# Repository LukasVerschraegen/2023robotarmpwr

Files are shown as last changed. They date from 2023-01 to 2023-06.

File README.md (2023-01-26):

# 2023robotarmpwr

Doelstelling:
ontwerpen en programmeren van een robotarm. En het ontwerpen yan dels stüring voor de steppermotoren
Het
op basis van een micro controlletalie draadloos kan bediend worden. En eventueel een extra display kan worden
toegevoegd ter visualisatie van de instelbare parameters.
De robot zal een automatisatierobot zijn die éénmalig wordt ingesteld en zo repetitive taken kan uitvoeren. Je kan
verschillende taken en cyclussen aanmaken die dan kunnen worden geselecteerd uit het menu op het display. Het
instellen van een cyclus kan handmatig gebeuren via het display, of via code.De volledige constructie van de
robot zal worden uitgewerkt met de 3D-printer,

Verplichte onderdelen rapport:

Kaft (voorblad)                                                                                              (gebruik de recentste logo's)
Abstract (in het Engels en informatief)
Inhoudsopgave                                                                                             
Codefragmentenlijst                                                                                           
Figurenlijst
Tabellenlijst
Afkortingenlijst
Inleiding                                                                                                        
1 Hoofdstuktitel                                                                                             
2 ...                                                                                                                 
3 ...
4 ...                                                                       
Conclusie
Handleiding   (enkel verplicht indien laboproeven moeten geschreven worden, dan horen ze hier / indien het project in gebruik genomen zal worden, schrijf dan een handleiding)
Literatuurlijst
Bijlagenoverzicht  (opmaak zoals inhoudsopgave)
Bijlage 1: Kopieën datasheets
Bijlage 2: Vergaderverslagen
Bijlage 3:  Logboek rapporteren

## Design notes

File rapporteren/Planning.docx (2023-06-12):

## Academiejaar: 2022 / 2023

Planning PWR:

Verslaggever: Lukas Verschraegen, Lennert De Geeter, Jorik Van Dorpe, Roy De Volder

Klas: 3ELO

Lector: Mario Wyns

Lesweek 9: 27/02 - 5/03

Naam student: | Doel:
Lennert De Geeter | Ontwerp 3d print/mechanica
Roy De Volder | Componenten zoeken
Jorik Van Dorpe | Componenten zoeken
Lukas Verschraegen | Componenten zoeken

Lesweek 10: 6/03 - 12/03

Naam student: | Doel:
Lennert De Geeter | Ontwerp 3D print/mechanica
Roy De Volder | Componenten zoeken
Jorik Van Dorpe | Componenten zoeken
Lukas Verschraegen | Componenten zoeken

Lesweek 11: 13/03 - 19/03

Naam student: | Doel:
Lennert De Geeter | Ontwerp 3D print/mechanica
Roy De Volder | Componenten bestellen
Jorik Van Dorpe | Componenten bestellen
Lukas Verschraegen | Componenten bestellen

Lesweek 12: 20/03 - 26/03

Naam student: | Doel:
Lennert De Geeter | 3D prototyping
Roy De Volder | Mee helpen opstaren van schema
Jorik Van Dorpe | Starten van Programmatie
Lukas Verschraegen | Starten van schema

Lesweek 13: 27/03 - 2/04

Naam student: | Doel:
Lennert De Geeter | 3D prototyping
Roy De Volder | 3D print ontwerp helpen printen
Jorik Van Dorpe | Verder werken aan programmatie
Lukas Verschraegen | Verder werken aan schema

Lesweek 14: 3/04 - 9/04

Naam student: | Doel:
Lennert De Geeter | Printen + assemblage in 3D ontwerp
Roy De Volder | Pcb-design opstarten
Jorik Van Dorpe | Verder werken aan programmatie
Lukas Verschraegen | Afwerken schema

Lesweek 15: 10/04 - 16/04

Naam student: | Doel:
Lennert De Geeter | Printen + assemblage in 3D ontwerp
Roy De Volder | Verder werken aan pcb
Jorik Van Dorpe | Tussentest programma
Lukas Verschraegen | Afwerken schema

Lesweek 16: 17/04 - 23/04

Naam student: | Doel:
Lennert De Geeter | Printen + assemblage in 3D ontwerp
Roy De Volder | Verder werken pcb /opsturen
Jorik Van Dorpe | Tussentest programma
Lukas Verschraegen | Helpen afwerken pcb/ opsturen

Lesweek 17: 24/04 - 30/04

Naam student: | Doel:
Lennert De Geeter | Assemblage bouten en moeren
Roy De Volder | Wachten op printplaat = controle van elkaars werk en verder werken verslag
Jorik Van Dorpe | Wachten op printplaat = controle van elkaars werk en verder werken verslag
Lukas Verschraegen | Wachten op printplaat = controle van elkaars werk en verder werken verslag

Lesweek 18: 1/05 - 7/05

Naam student: | Doel:
Lennert De Geeter | Testen zonder motoren (alles draait)
Roy De Volder | Printplaat bestukken
Jorik Van Dorpe | Opstarten en testen pcb/ programmatie
Lukas Verschraegen | Opstarten en testen van pcb

Lesweek 19: 8/05 - 14/05

Naam student: | Doel:
Lennert De Geeter | Testen met motoren
Roy De Volder | Testen/ debuggen pcb
Jorik Van Dorpe | Testen/ debuggen code
Lukas Verschraegen | Testen/ debuggen schema

Lesweek 20: 15/05 - 21/05

Naam student: | Doel:
Lennert De Geeter | Herontwerp + assemblage
Roy De Volder | Testen/ debuggen + oplossen bugs en metingen
Jorik Van Dorpe | Testen code + oplossen bugs
Lukas Verschraegen | Testen/ debuggen + oplossen bugs en metingen

Lesweek 21: 22/05 - 28/05

Naam student: | Doel:
Lennert De Geeter | Finale test
Roy De Volder | Finale test
Jorik Van Dorpe | Finale test
Lukas Verschraegen | Finale test

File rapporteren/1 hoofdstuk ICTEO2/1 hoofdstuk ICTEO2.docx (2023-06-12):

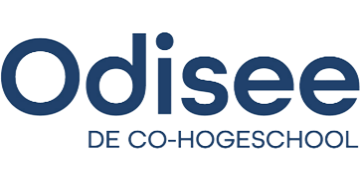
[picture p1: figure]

Professionele bachelor Elektronica-ICT

Academiejaar: 2022 / 2023

# Het maken en sturen van een robotarm

Lectoren: Sabine Martens
Mario Wyns

Verslaggevers: Lennert De Geeter
Roy De Volder
Jorik Van Dorpe
Lukas Verschraegen

Klas: 3ELO

Professionele bachelor Elektronica-ICT

Academiejaar: 2022 / 2023

# Het maken en sturen van een robotarm

Lectoren: Sabine Martens
Mario Wyns

Verslaggevers: Lennert De Geeter
Roy De Volder
Jorik Van Dorpe
Lukas Verschraegen

Klas: 3ELO

Abstract

Inhoudsopgave

Figurenlijst

Tabellenlijst

Afkortingenlijst

Tabel 1: Afkortingenlijst

Afkorting | Betekenis
BOM | Bill of Materials
IC | Integrated circuit
DC | Direct current
PWM | Pulse-width modulation
MCU | Microcontroller unit
ESC | Electronic speed control
NEMA | National Electric Manufacturers' Association
pcb | Printed circuit board
IoT | Internet of Things
SoC | System-on-chip
SPI | Serial Peripheral Interface
I2C | Inter-Integrated Circuit
UART | Universal asynchronous receiver-transmitter
BLE | Bluetooth Low Energy
USB | Universal Serial Bus
LDO | Low-dropout
TTL | Transistor-Transistor Logica
RMS | Root Mean Square
DIR | Direction
OTP | One-time programmable
SRAM | Static random-access memory

Begrippenlijst

Tabel 2: Begrippenlijst

Begrip | Verklaring
Brushless | Geen gebruik maken van fysieke contacten naar de commutator van de motor.
Flash | Flash is de verzamelnaam voor opslagsystemen waar data wordt opgeslagen op chips die hun informatie behouden nadat de voedingsspanning is weggehaald. Het is een vorm van niet-vluchtig geheugen dat in 1984 voor het eerst op de markt kwam.
SRAM | Static random-access memory is een geheugen waarvan de inhoud niet periodiek geüpdatet hoeft te worden. De opgeslagen data in een SRAM kunnen te allen tijde en in elke volgorde worden uitgelezen en wijzigen enkel als ze worden overschreven of als de IC spanningsloos wordt. Het is dus een vluchtig geheugen.
Pinout | Een pinout is een verwijzing naar de pinnen of contacten die een elektrisch apparaat of connector verbinden. Het beschrijft de functies van uitgezonden signalen en de circuit input/output (I/O) vereisten.
Royaltyvrij | Royaltyvrij is een term die wordt gebruikt om bepaalde soorten intellectuele eigendom te beschrijven zonder royalty's te betalen. Eigenaars van intellectuele eigendom moeten dit label specifiek op hun inhoud toepassen, zodat iedereen het op dezelfde manier kan gebruiken.
Beheersmaatregelen | Beheersmaatregelen zijn de maatregelen die genomen worden om de risico's waaraan ondernemingen blootstaan te beheersen.
Consciëntie | Nauwkeurigheid.
SCARA | Selective Compliance Articulated Robot Arm

Inleiding

In dit project wordt een prototype van een robotarm ontworpen en ontwikkeld. De arm moet met toegankelijke hardware en machines vervaardigd kunnen worden. De robotarm wordt ontworpen binnen een industriële omgeving waar hij repetitieve taken precies zal moeten uitvoeren.

In een eerste hoofdstuk wordt onderzoek gedaan naar de verschillende mogelijkheden van de arm. Die kan namelijk mechanisch uit heel wat verschillende ontwerpstrategieën bestaan. Ook kan afhankelijk van de toepassing en de grijpfunctionaliteit andere tooling nodig zijn. De robotarm wordt logischerwijze gestuurd door motoren, ook hier zijn weer een aantal mogelijkheden met voor- en nadelen. De robotarm is een prototype voor in een industriële omgeving, ook veiligheid is dus een aandachtspunt.

Eens de basiseigenschappen in het onderzoek zijn uitgeklaard, kan al deze kennis in het ontwerp worden overgenomen. Dat is dan ook het volgende hoofdstuk van dit onderzoek en omvat zowel een mechanisch als elektronisch ontwerp. Delen zoals een blokschema, componenten, Bill of Materials en elektronische schema’s, alsook een finaal mechanisch ontwerp worden in dit tweede hoofdstuk besproken.

Eens alle ontwerpen en onderzoeken zijn uitgevoerd, kan worden overgegaan tot de realisatie van de arm. In het derde hoofdstuk wordt de bestukking van de PCB besproken en de programmatie ervan. Ook het 3D-printen van de arm en zijn assemblageproces komen hier aan bod.

Wanneer de robotarm tot slot dan volledig geassembleerd is, kan de testfase worden ingezet. In dit vierde hoofdstuk worden functionaliteit en veiligheid extra onder de loep genomen en eveneens het oplossen van problemen met mechanische onderdelen en programmatie.

Via een experimentele onderzoeksmethode wordt dit project en dossier opgebouwd. De belangrijkste bronnen zijn datasheets van de componenten en diverse online bronnen en ontwerpen.

# 1 Onderzoek

Om vlot van start te gaan met het project is het belangrijk om voorkennis te hebben van de onderdelen van een robotarm.

In dit hoofdstuk worden verschillende onderdelen vergeleken die noodzakelijk zijn om een robotarm te laten functioneren. De focus ligt vooral op de realiseerbaarheid en het gebruiksgemak van verschillende producten. Vooraleer een ontwerp van toepassing is, is vergelijken van producten noodzakelijk om te weten wat haalbaar is. Kosten en gebruiksgemak zijn hierbij uiteraard belangrijk.

De motoren, sensoren, het mechanische deel van de robotarm, de veiligheid en tot slot het opzetstuk van de robotarm zijn de belangrijkste onderdelen van dit project. Dit is de reden waarom er naar elk onderdeel onderzoek zal gebeuren. Om verschillende materialen te verplaatsen zijn immers andere en eventueel nauwkeurigere opzetstukken nodig. Hierdoor wordt het belang van de vervangbaarheid van een opzetstuk benadrukt.

## 1.1 Motoren

Motoren zijn een hoofdzaak bij het ontwerpen van een robotarm. Waarmee rekening moet gehouden worden, is dat bij de basis van de robotarm een zware motor mag gebruikt worden. Op het einde van de robotarm zullen lichtere motor gekozen worden die nog steeds krachtig genoeg zijn om een bepaald gewicht te heffen.

Als er zware motoren op het einde van de arm zouden hangen, dan zou de robotarm dat gewicht ook moeten heffen. Aangezien motoren zijn opgebouwd uit spoelen en vaak uit een metalen kern, is dit wel degelijk van belang want deze elementen beïnvloeden het gewicht snel.

De beweeglijkheid van een motor is belangrijk, een vloeiende beweging is een onderdeel waar naar gekeken wordt. Uiteraard is dit eveneens afhankelijk van de sensoren waarmee de motor wordt aangestuurd. Vandaar het gebruik van motoren die gemakkelijk compatibel zijn met een IC. Om kracht in de motor te behouden wordt er bekeken of er intern tandwielen zijn geplaatst.

Naast de vooraf besproken aspecten speelt ook de kostprijs – die varieert naargelang de grootte van de motor- een grote rol. Hoe groter de motor, hoe hoger de prijs zal zijn, want hoe groter de motor, hoe meer koper er gebruikt wordt, en koper is duur. Energiezuinig is een motor meestal niet, maar dit is wel belangrijk.

Er bestaan verschillende motoren zoals: stappenmotoren, servomotoren, DC motoren en brushless DC motoren. Bekijk de vergelijking en de uitleg van de meest voorkomende motoren in de elektronica in onderstaande Tabel 3.

De vergeleken motoren zijn geselecteerd op basis van populariteit en kracht:

### 1.1.1 Stappenmotor

Als er gekeken wordt naar kracht en populariteit, dan wordt er vaak gebruik gemaakt van een NEMA 17 motor, de motor is vooral populair in toepassingen met de 3D-printer [1].

### 1.1.2 Servomotor

Bij een servomotor is kracht een grote factor, een motor die 25 kg kan heffen is dus de beste keuze. De td-8125mg is dus een veel gebruikte optie en is hier de beste mogelijkheid [2].

### 1.1.3 DC motoren

Voor DC motoren wordt er gesproken van een transmissiemotor, het woord transmissie spreekt voor zich, er is namelijk een tandwieloverbrenging aanwezig [3].

### 1.1.4 Brushless DC motoren

Aangezien de brushless DC motoren van oorsprong weinig gewicht kunnen dragen, is de populariteit van belang. Drone motoren, zoals de Pichler motor, zijn de meest gebruikte in hun soort [4].

De conclusie uit Tabel 3 is dat er in dit project een combinatie zal worden gebruikt van stappenmotoren en servomotoren. De brushless DC motor en de DC motor hebben allebei een continue beweging, wat niet ideaal is, en worden om die reden niet in dit project gebruikt.

Tabel 3: Vergelijking van motoren

| Stappenmotoren | Servomotoren | DC motoren | Brushless DC motoren
Beweging | Een stappenmotor kan verschillende posities aannemen. Er is een vloeiende beweging om van de ene positie naar de andere te gaan. De verandering gebeurt heel snel en precies. | Een servomotor heeft een vloeiende beweging bij het verdraaien, maar is niet altijd even precies doordat sommige motoren plastic tandwielen hebben. Het voorbeeld is daarom met metalen tandwielen. | De vloeiende beweging van een DC motor draait constant in eenzelfde richting. Voor de robotarm is de DC motor niet geschikt aangezien er een positie moet worden bepaald. | Een brushless DC motor is een motor die heel vloeiend draait, maar hij heeft ook een continue beweging zoals de normale DC motor. Er is ook een speciale sturing nodig om controle te krijgen over de snelheid.
Gewicht motor | 280 g | 62 g | 200 g | 29 g
Hefkracht | 4,0 kg/cm | 25 kg/cm | 75 kg/cm | 730 g/cm
Kostprijs | € 11 | € 11,5 | € 12 | € 27,99
Tandwielen | Er zijn geen ingebouwde tandwielen aanwezig. | De motor in het voorbeeld heeft ingebouwde, metalen en robuuste tandwielen om aan een groot hefvermogen te komen. | De motor in het voorbeeld heeft ingebouwde, metalen en robuuste tandwielen om aan een groot hefvermogen te komen. | Er zijn geen ingebouwde tandwielen aanwezig.
Draaihoek | Er is een staphoek van 1,8° per stap. | 0-180° aangestuurd met een PWM-signaal. | Een DC motor heeft altijd een continue draaihoek, en is dus niet instelbaar. | Een brushless DC motor heeft altijd een continue draaihoek, en is dus niet instelbaar.
Stroom | 1,7 A | 3,4 A | 200 mA | 23 A
Aanstuurbaarheid | Aangezien er meerdere spoelen gebruikt worden in de motor is er een bepaalde IC nodig om ze aan te sturen. | De servomotor heeft de mogelijkheid om via PWM aangestuurd te worden. Dit is gemakkelijk omdat bijna elke MCU dit signaal kan genereren. | Deze motor kan aangestuurd worden door voeding op de motor te zetten, dit werkt zonder enig stuursignaal. | Om aan te sturen heeft de brushless DC motor een ESC nodig.
Aansluitbaarheid | Deze motor heeft een dikke en stevige as van 5 mm diameter om iets op aan te sluiten. Een veel gebruikte motor is een NEMA 17 motor met standaard montagepunten. | De motor heeft een metalen as met ribbels om betere grip te krijgen en een hol center waar je een schroef kan indraaien. De aansluiting is dus heel sterk en stevig. Een nadeel is dat de diameter van de as redelijk klein is. Er zijn twee montagepunten aanwezig. | De aansluitbaarheid bij deze DC motor is super, hij heeft een D-vormige as voor ultieme krachtoverbrenging. De asdiameter is 6 mm en de motor zelf heeft geen montagepunten. | De motor kan je goed koppelen aan onderdelen doordat hij een stevige metalen as heeft met een diameter van 15 mm. Hierop zit nog een bevestigingsstuk dat kan worden vastgeschroefd. De motor heeft vier montagepunten.

## 1.2 Sensoren

Sensoren zijn van groot belang bij een robotarm. Vooraleer de sensoren iets kunnen lezen of sturen, moet er een microcontroller worden gezocht. De MCU stelt het brein van de pcb voor en is extreem belangrijk.

Er bestaan verschillende modellen microcontrollers. Aangezien een wificonnectie belangrijk is om bijvoorbeeld data te sturen naar een website, zijn er enkele microcontrollers die gebruik maken van ingebouwde antennes. Deze laatste worden gebruikt bij Internet of Things (IoT) applicaties.

Er zal een vergelijking worden gemaakt tussen de twee populairste MCU’s van de grootspelers op de markt, namelijk Arduino met “Arduino mkr wifi 1010” [5] en Espressif met ”ESP32” [6].

Aangezien de ESP-boards open source zijn, zijn er ook andere fabrikanten die gelijkaardige system on a chip (SoC) microcontrollers verkopen.

De ESP-boards kunnen zowel voor professionele als amateuristische toepassingen gebruikt worden. De boards zijn open source en op die manier is het gemakkelijk om te achterhalen hoe ze geprogrammeerd kunnen worden.

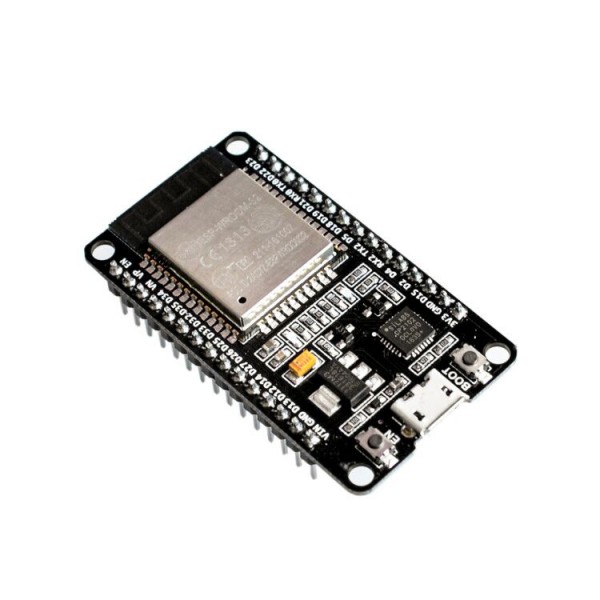
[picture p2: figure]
ESP32 WiFi and Bluetooth Board - CP2102
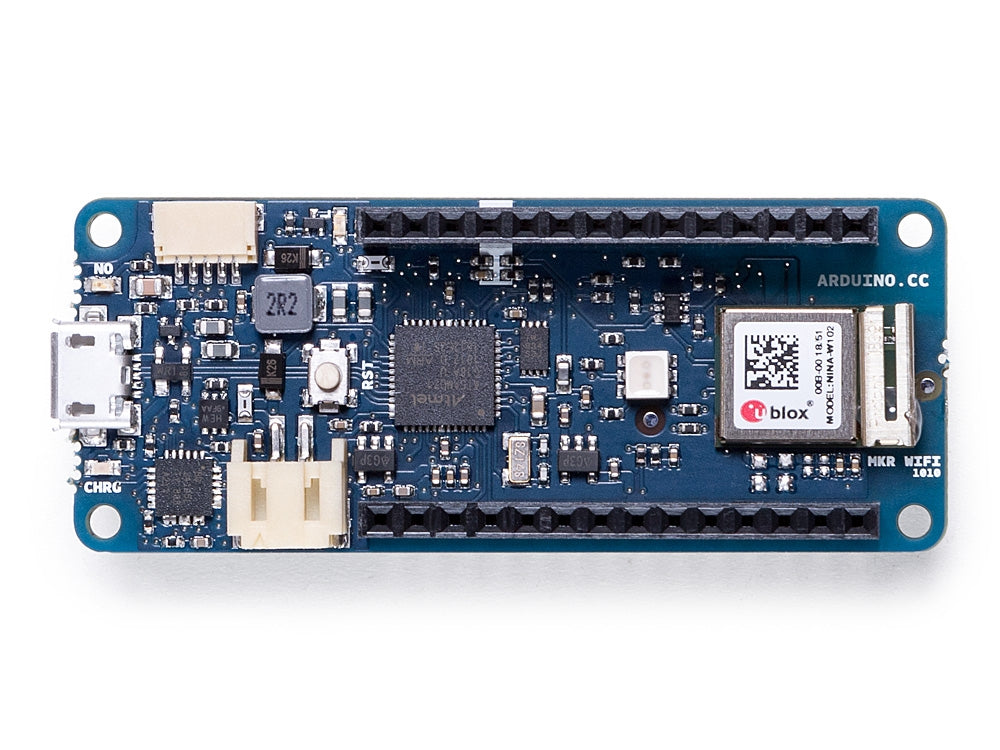
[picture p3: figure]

Figuur 2: ESP32

Figuur 1: Arduino mkr wifi 1010

Figuur 2: ESP32

Tabel 4: Microcontrollers vergelijken

Fabrikant | Arduino | | Espressif
Product | Mkr wifi 1010 | | ESP32
Chip | ATSAMD21 | | ESP32-WROOM-32D
Geheugen | FLASH: 256 kB | SRAM: 32 kB | FLASH: 4 MB | SRAM: 520 kB
Interface | SPI/ I2C/ UART | | SPI/ I2C/ UART
Wifi | Ja | | Ja
BLE | Neen | | Ja
Voltage | 5 V input | 3,3 V output | 5 V input | 3,3 V output
Pinout | Digitaal/ analoog/ PWM | | Digitaal/ analoog/ PWM
Afmetingen | 61,5 mm x 25 mm | | 52 mm x 28 mm
Prijs | € 33,50 | | € 9,50

Wat direct opvalt bij de vergelijking is de prijs, de Arduino microcontroller is veel duurder. De rest van de eigenschappen is zo goed als gelijk. Bij de Espressif variant is het geheugen beter én is er de mogelijkheid om voor die goedkopere prijs zelfs BLE te hebben.

Er hoeft niet langer getwijfeld te worden, de keuze gaat naar Espressif als het op MCU’s aankomt. De ESP32 is een heel goed ondersteunde microcontroller om de nodige doeleinden waar te maken. Dit hoeft niet precies de ESP-WROOM-32 te zijn, maar kan ook een variant zijn binnen deze familie, aangezien de meeste eigenschappen gedeeld worden.

Nu de chip gevonden is, is het belangrijk om te weten welke sensoren compatibel zijn met deze MCU’s.

Er zal eerst gekeken worden hoe een ESP32 van spanning zal voorzien worden als er enkel met de chip zelf [7] gewerkt wordt, een voorstelling van de chip ziet u hieronder in Figuur 3.

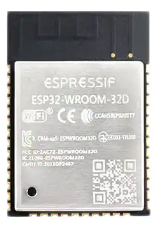
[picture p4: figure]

Figuur 3: ESP32-WROOM-32D chip zonder pcb

### 1.2.1 Voeding

Vroeg of laat zal er USB-C moeten worden gebruikt voor elk nieuw elektrisch apparaat op de handelsmarkt volgens volgende bron van het Europees parlement [8]. Dit zou van start gaan in de herfstperiode van 2024 en zou vanaf dan langzaam moeten ingeburgerd worden.

Dit is dan ook direct een goede reden om de USB-C te implementeren in het project. De connector heeft als eigenschap dat hij gebruiksvriendelijk is. Het maakt niet uit in welke richting de kabel wordt aangesloten, communicatie en voeding met het apparaat is er direct via de 24 pins-connector. Het grote voordeel van USB-C is dat er een hogere datatransmissiesnelheid is en een hogere stroomvoorziening van 100 W bij 20 V en 5 A. Een voorstelling van zo een connector ziet u in Figuur 4

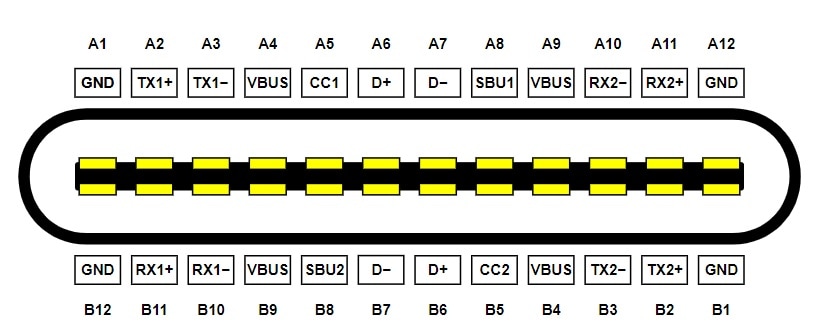
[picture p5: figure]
What is USB C? USB C Plug & Receptacle Pinouts | Arrow.com | Arrow.com

Figuur 4: USB-C pinout

De voorstelling hierboven (Figuur 4) geeft de pinnen weer voor elk mogelijk protocol. Er zijn dan ook verschillende protocollen zoals Thunderbolt, Displayport, HDMI en USB die USB-C ondersteunen. Belangrijk voor communicatie met de ESP-chip is het USB-protocol.

Om de ESP te voeden, is het belangrijk dat die de juiste spanning krijgt. De chip wordt gevoed met een spanning van 3,3 V wat met een Low-dropout regulator (LDO) verkregen wordt.

Dit is een lineaire DC-spanningsregelaar die de uitgangsspanning stabiel kan regelen op 3,3 V.

Het systeem werkt volgens het principe met potentiaalverschil tussen input en output, dit wil zeggen dat de ingang altijd hoger moet zijn dan de uitgang. Het energieverlies tussen deze twee spanningen wordt omgezet in warmte.

Er is geen verklaring voor de specifieke waarde van de condensatoren die rond een LDO staan (te zien in Figuur 5). De elektrolytische condensatoren dienen in een schakeling als spanningsbuffer, dit wil zeggen dat er nog steeds een kleine spanning aanwezig is als de algemene spanningsbron plots wegvalt in het circuit.

Keramische condensatoren zijn meestal heel laag van capaciteit en worden bij een LDO gebruikt als ontkoppelcondensatoren. Die dienen om ruis te filteren dat aanwezig is in een schakeling. [9]

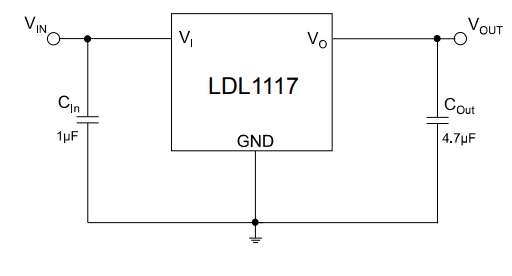
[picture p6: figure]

Figuur 5: Typische applicatie LDO

### 1.2.2 Communicatie

Om te communiceren met een ESP-32 moet er een aparte chip worden gebruikt. Eén van de veel gebruikte mogelijkheden is de CP2102. Uit de USB-C poort komt een protocol dat USB heet, maar dit verstaat de ESP-32 niet. Wat de ESP wel verstaat is het UART protocol. Dit is de reden waarom gedacht wordt aan de veel gebruikte CP2102, het is namelijk een USB naar TTL Serial UART convertor.

TTL staat voor Transistor-Transistor Logica. Hieruit kan er worden afgeleid dat het een chip is op basis van transistoren. Waar TTL ook om bekend staat, is dat het spanningsniveau van 0 tot 5 V heeft.

Wat een groot voordeel is aan de CP2102, is dat het een complete plug-and-play interface-oplossing biedt met royaltyvrije stuurprogramma's. De chip is USB 2.0-compatibel wat zorgt voor snelle communicatie.

### 1.2.3 Programmatiecircuit

Er is een resetknop en een flashknop (of bootknop) nodig om een programma op de microcontroller te laden. De functie van de resetknop dient om de enable pin van de MCU naar een ground te trekken, want standaard staat de enable pin op een hoog niveau. Als dit gebeurt, dan wijkt de chip af van zijn standaardprogramma, wordt het onderbroken en dus ook gereset.

Om programma’s in te laden kan er gebruik worden gemaakt van een simpel transistor netwerk om automatisch in te laden. Hiervoor is geen knop meer nodig. Als dit netwerk niet aanwezig is, zal tijdens het inladen van het programma op de flashknop moeten worden geduwd.

### 1.2.4 Sensor voor het aansturen van de stappenmotor

TMC2208 is een ultrastille tweefasige stappenmotor driver chip [10]. Het stuurt de motoren aan door full step en microstepping. TRINAMIC's geavanceerde stealthChop2 technologie zorgt voor een geruisloze werking, maximale efficiëntie en het beste motorkoppel. De snelle stroomregeling en de optionele combinatie met spreadCycle zorgen voor een zeer dynamische beweging.

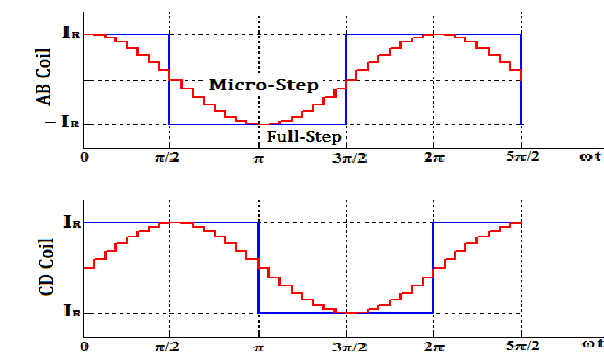
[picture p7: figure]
Variable rate based microstepping of stepper motor using MATLAB GUI | Semantic Scholar

Figuur 6: Full-step vs. micro-step

De bedoeling van microstepping is het omzetten van de blokgolf die de motor aanstuurt naar een sinusgolf. Een perfecte sinusgolf wordt nooit behaald maar de TMC2208 komt, in vergelijking met de A4988 en andere chips, er het dichtste bij. Dit komt omdat het gebruik maakt van 1/256 microstepping. Hierdoor worden de stappen zeer klein en worden er minimale trillingen gegenereerd, waardoor deze chip de motor zeer stil doet draaien.

Zonder microstepping maakte bijvoorbeeld een 4-stappenmotor vier stappen per volledige aswenteling (dus 90° per stap). Door gebruik te maken van een 1/256 microstepping worden de motorspoelen zo aangestuurd dat er 4*256=1024 stappen nodig zijn om een volledige omwenteling te maken (dus 0,3515625° per microstap).

Eigenschappen [11]:

- Aandrijfcapaciteit tot 1,2 A (RMS) continue spoelstroom - 2 A piek
- STEP/DIR-interface met 2, 4, 8, 16 of 32 microstep pininstelling
- 256 microstappen door microPlyer™-interpolatie
- StealthChop2 voor stille werking en vloeiende bewegingen (standaardinstelling)
- SpreadCycle zeer dynamische motorbesturing chopper (schakelbaar via UART)
- Voedingsspanning motor: 5,5 tot 36 V
- Logische voedingsspanning: 3,3 tot 5 V
- Automatische stand-by stroomreductie (optie)
- Passief remmen en vrijloop
- Single Wire UART& OTP voor geavanceerde configuratie-instellingen
- Geïntegreerde pulsgenerator voor zelfstandige beweging

Een andere keuze om de motoren aan te sturen is de A4988 microstepping stappenmotor driver. Het voordeel van deze chip is dat deze een beetje goedkoper is. Het nadeel en de reden waarom deze chip niet gebruikt wordt, is dat de motoren veel meer lawaai maken.

## 1.3 Mechanica

In een vorig hoofdstuk werden de verschillende types motoren al besproken. Zoals werd bekeken heeft ieder type motor een verschillende draagkracht, en is die dus ook beter toepasbaar op verschillende punten.

Bij industriële armen wordt voor de scharnierpunten gebruik gemaakt van stappenmotoren en servomotoren. Afhankelijk van het type motor is een andere mechanische ontwerpstrategie nodig. Het prototype, besproken in dit dossier, zal worden uitgewerkt met een 3D-printer, ook dat is een belangrijk punt om rekening mee te houden. De verschillende mogelijkheden met deze eigenschappen kunnen worden opgedeeld in drie groepen.
Deze groepen bestaan uit een cartesische, een articulated en een SCARA-robotarm, waarvan hieronder een afbeelding. Figuur 7 [12]

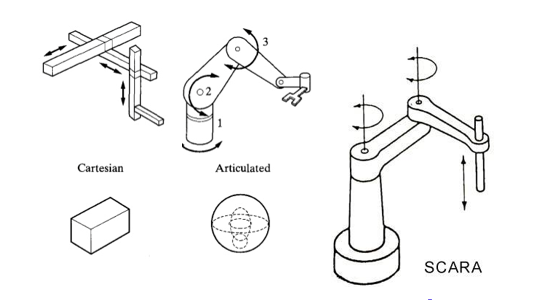
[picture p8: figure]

Figuur 7: Verschillende types robotarmen

### 1.3.1 Cartesische robotarm

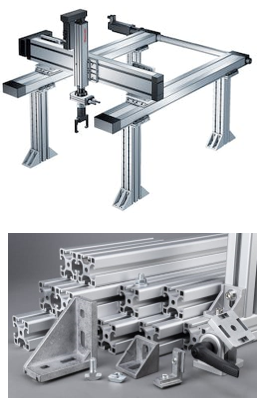
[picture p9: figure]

De cartesische robot gelijkt het meeste op een klassieke CNC-machine of 3D-printer. Cartesische of lineaire robots werken op drie assen: X,Y en Z. Deze drie assen maken een beweging mogelijk van links naar rechts, van voor naar achter en van boven naar beneden. Door de specifieke opbouw van dit type robot is hij erg flexibel. Zo kan die afhankelijk van de toepassing snel en eenvoudig worden aangepast. Deze hoge flexibiliteit is te danken aan de typerende aluminiumprofielen waaruit de robot is opgebouwd. Deze profielen zijn internationaal verkrijgbaar in verschillende lengtes en breedtes en laten zich erg makkelijk bewerken. Hierdoor kunnen lagers, geleiders, … makkelijk en snel worden gemonteerd. Door deze standaardprofielen kan ook de prijs van een cartesisch systeem erg aantrekkelijk zijn. Figuur 8 [13][14]

Figuur 8: Cartesische robotarm en de aluminium profielen

Een mogelijke toepassing van dit ontwerp is het open source LumenPnP project door Opulo. Figuur 9 [15]

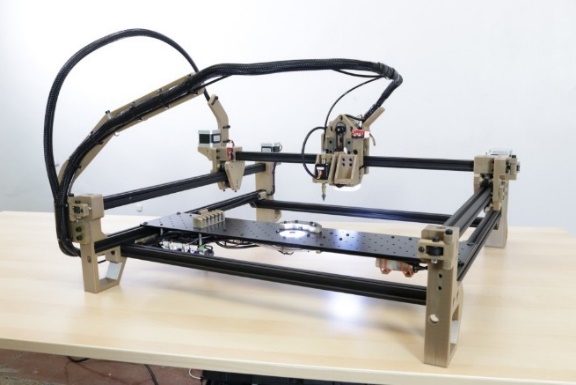
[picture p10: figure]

Figuur 9: LumenPnP cartesische robotarm

Deze machine maakt het voor iedereen mogelijk een pcb op één niveau met hoge precisie te bestukken. De machine beweegt op de drie assen in rechte lijnen, een toepassing waar de cartesische robot uiterst geschikt voor is.

Zoals al eerder vermeld moet het volledige werkgebied worden omkaderd. Dit is een nadeel voor de robot die in dit onderzoek wordt gemaakt, aangezien bewegingsvrijheid een belangrijk punt is.

### 1.3.2 Articulated robotarm

Een derde type is de articulated of vrijdraaiende robot. Dit type robot gelijkt het best op een menselijke arm met alle bijbehorende voordelen. Deze robotarm wordt gemonteerd op een draaiende basis. Met een basisaantal motoren kan de volledige 3D-ruimte rondom de arm worden bereikt. Naarmate meer motoren en assen worden toegevoegd, wordt de toegankelijkheid van dit gebied nog verbeterd. Dit type robot kent een wijde inzetbaarheid in de industrie; van taken zoals lassen en materialen verplaatsen tot volledige assemblage en inpakken. Figuur 10 [17]

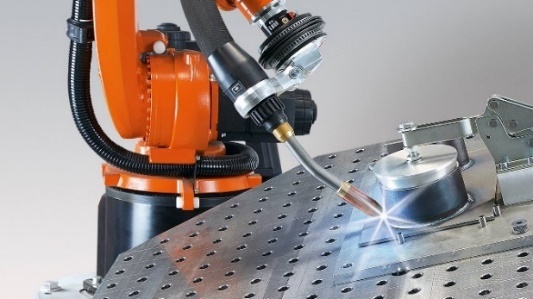
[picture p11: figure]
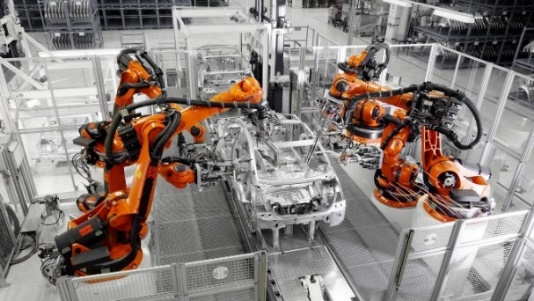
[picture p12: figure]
HRC system at BMW's production plant | KUKA AG

Figuur 10: Lasrobot Figuur 11: Assemblagerobot

Eén van de voordelen van dit ontwerp is de centrale basis waar de hele arm op draait. In dit onderzoek brengt dit een belangrijk punt met zich mee, namelijk dat het volledige gewicht op één centrale motor en as terechtkomt. De andere motoren werken wel mee aan de beweging, op voorwaarde dat de onderste as die kan ondersteunen.

Om dit allemaal mogelijk te maken zijn overbrengingen op de motoren erg belangrijk.

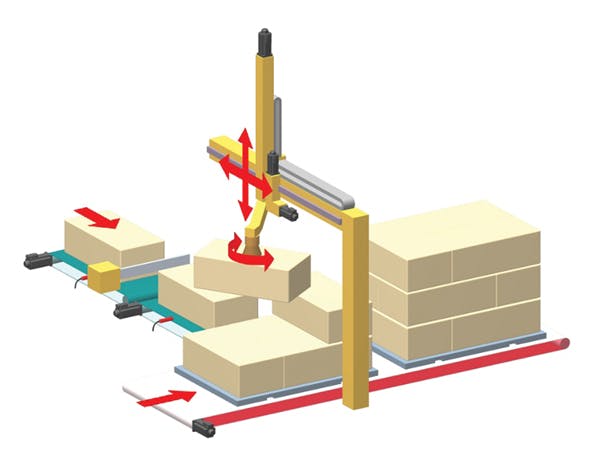
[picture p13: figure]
Machinedesign Com Sites Machinedesign com Files Uploads 2013 09 121213 1 Cartesian Robots

### 1.3.3 SCARA-robotarm

Het SCARA-ontwerp heeft net zoals de cartesische robot drie assen waarop die beweegt. Het verschil tussen beide zit echter tussen de manier waarop wordt bewogen. Het cartesische ontwerp doet dat telkens in een hoek van 90°, terwijl een SCARA-robot om zijn eigen as kan draaien. Dat maakt dit ontwerp uiterst geschikt voor het stapelen van dozen of voor assemblage. Figuur 12 [13]

Figuur 12: Scara-robotarm

Voor dit ontwerp zijn verschillende open source toepassingen beschikbaar. Bijvoorbeeld dit type door PyBot. [16]

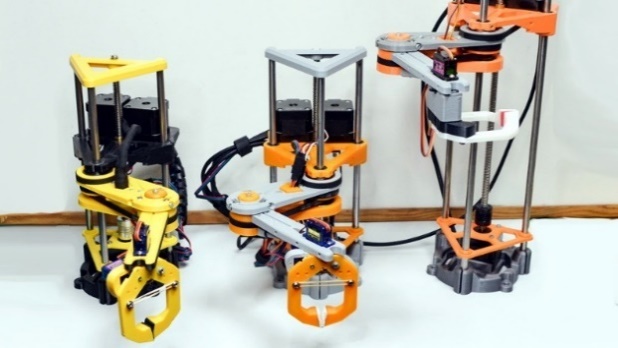
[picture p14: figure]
PyBot Is A 3D Printed SCARA Arm For The Masses | Hackaday
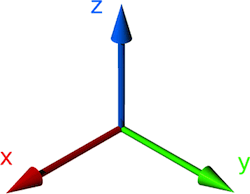
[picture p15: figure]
want Z axis is up not Y axis, second contour problem | WPF Chart Forums

Figuur 13: Uitgewerkt versie PyBot Figuur 14: 3D-Assenstelsel

Het is opnieuw volledig uitgewerkt op een 3D-printer met standaardcomponenten erin verwerkt. Dit type geeft door zijn enkele roterende basis een beter beeld van de toepassing in dit onderzoek. Hij is gelimiteerd in de bewegingen die kunnen worden gemaakt. Zo is iedere beweging in de Z-richting of hoogte afhankelijk van één motor. Figuur 13

## 1.4 Veiligheid

Bij het ontwerpen en realiseren van een robotarm zijn verschillende aspecten van veiligheid van belang. Het uitvoeren van een goede risicoanalyse is hierbij cruciaal om mogelijke gevaren te identificeren die zich kunnen voordoen tijdens het gebruik van de robotarm. Het is daarbij van belang om potentiële gevaren voor zowel de bediener als andere personen in de omgeving van de robotarm te evalueren.

Stap één van de risicoanalyse omvat de identificatie van mogelijke gevaren, zoals snelle bewegingen van de robotarm die letsels kunnen veroorzaken, hoge temperaturen bij het gebruik van de robotarm, blootstelling aan elektrische stroom en mogelijke botsingen met personen of objecten in de buurt.

Stap twee van de risicoanalyse omvat de evaluatie van de waarschijnlijkheid dat de gevaren zich zullen voordoen en de mogelijke ernst van de gevolgen als ze zich voordoen. Op basis hiervan kan worden bepaald welke risico’s prioriteit hebben bij het nemen van beheersmaatregelen.

Stap drie van de risicoanalyse omvat het identificeren van beheersmaatregelen om de risico’s te verminderen of te elimineren. Dit kan bijvoorbeeld worden bereikt door het installeren van fysieke barrières rondom de robotarm of door gebruik te maken van sensoren die de robotarm kunnen stoppen wanneer een persoon in de buurt komt. Het is daarbij van belang om noodstoppen te installeren die de robotarm onmiddellijk stoppen wanneer er een onverwachte situatie ontstaat. Verder moeten alle gebruikers van de robotarm getraind zijn om veilig gebruik te maken van de robotarm en bijhorende apparatuur. Ook regelmatig onderhoud en inspectie zijn belangrijk om preventief te kunnen handelen.

Door rekening te houden met deze factoren en andere belangrijke veiligheidsaspecten, kunnen ontwerpers en gebruikers ervoor zorgen dat de robotarm veilig en efficiënt werkt.

## 1.5 Opzetstuk

Eén van de belangrijkste aspecten bij het maken van een robotarm is het ontwerpen van de opzetstukken. Een opzetstuk is het deel van de robotarm dat in contact komt met het object dat wordt verplaatst of bewerkt. Het type opzetstuk dat wordt gebruikt, hangt af van de toepassing en het gewenste resultaat.

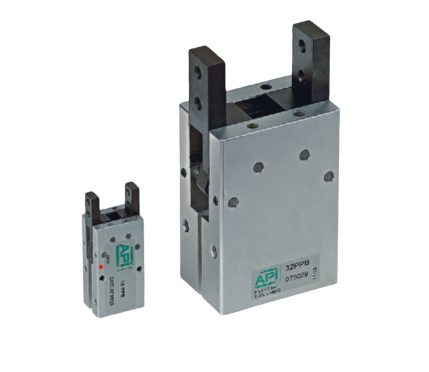
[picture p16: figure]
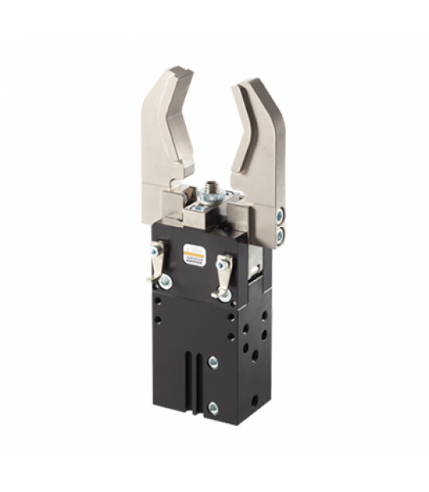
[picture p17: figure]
Pneumatische Grijpers - Robotgrijpers - ZVS Techniek

Eén van de meest voorkomende opzetstukken voor een robotarm is de grijper. Dit opzetstuk wordt gebruikt om objecten vast te pakken en te verplaatsen. Er zijn verschillende soorten grijpers, zoals parallelle grijpers, hoekgrijpers en pneumatische grijpers. Parallelle grijpers worden vaak gebruikt in industriële toepassingen, zoals het assembleren van producten, het verpakken van goederen of het laden en lossen van vrachtwagens. Ze zijn ook populair in laboratoriumomgevingen en in de gezondheidszorg voor het hanteren van delicate en gevoelige objecten. Over het algemeen bieden parallelle grijpers een betrouwbare en efficiënte manier om objecten vast te pakken en te hanteren met behulp van een robotarm.

Figuur 15: Parallelle grijper

Hoekgrijpers zijn een ander type grijper dat vaak wordt gebruikt. Zoals de naam al aangeeft, zijn hoekgrijpers ontworpen om objecten vast te pakken en vast te houden met behulp van een set vingers die in een hoek zijn gepositioneerd ten opzichte van elkaar. Dit type grijper wordt gebruikt in toepassingen waarbij het vast te pakken voorwerp niet plat of rechthoekig is, maar een onregelmatige vorm heeft. Pneumatische grijpers worden voornamelijk gebruikt voor het hanteren van delicate objecten zoals objecten die gemaakt zijn van glas of breekbaar materiaal.

Figuur 16: Pneumatische hoek-grijper

Een ander type opzetstuk is een lasersnijder. Dit opzetstuk gebruikt lasers om materialen te snijden. Het is vooral handig in industriële toepassingen waar precisie en snelheid van belang zijn, zoals bij het snijden van metaalplaten.

Schuurmachines zijn een andere soort veelvoorkomend type van opzetstuk voor een robotarm. Ze worden gebruikt om materialen te schuren en glad te maken. Dit type opzetstuk wordt het meest gebruikt in de automobiel- en meubelindustrie.

Een magnetisch opzetstuk wordt gebruikt om metalen voorwerpen op te tillen en te verplaatsen. Dit type opzetstuk is handig voor het hanteren van zware of gevaarlijke metalen voorwerpen. Dit kan bijvoorbeeld van pas komen in een fabriek waar zware metalen onderdelen worden geproduceerd. Het gebruik van een magnetisch opzetstuk kan de efficiëntie en productiviteit van de robotarm verbeteren. Het kan immers snel en gemakkelijk objecten oppakken en verplaatsen zonder dat er veel aanpassingen nodig zijn. Bovendien verkleint de kans op ongevallen door vallende voorwerpen omdat ze beter vasthangen aan de robotarm.

Het is ook mogelijk om camerasystemen te gebruiken als opzetstuk. Dit type opzetstuk wordt gebruik om beelden vast te leggen en te analyseren. Het wordt vaak gebruikt in de industrie voor kwaliteitscontrole, inspectie en robotica-onderzoek. Het camerasysteem kan er in combinatie met andere types opzetstukken voor zorgen dat bijvoorbeeld delicate voorwerpen beter gegrepen kunnen worden omdat er voorziening is van een beter beeld.

Men kan een robotarm ook uitrusten met een boormachine als opzetstuk om gaten te maken in materialen. Dit soort opzetstuk is ideaal voor situaties waarbij precisie, consciëntie en herhaalbaarheid van cruciaal belang zijn. Een robotarm met een boormachineopzetstuk kan ook worden gebruikt om schroeven te draaien in onderdelen die al voorzien zijn van schroefgaten. Dit vermindert de noodzaak van menselijke arbeid en verbetert de efficiëntie van het productieproces. Naast boren en schroeven kan de robotarm gebruik maken van een boormachineopzetstuk om een bepaald patroon in een materiaal te frezen.

De keuze in gebruik van het soort opzetstuk is belangrijk in het designproces van de robotarm. Hij kan op die manier volledig naar wens worden gemaakt en er kan eventueel extra gewicht toegevoegd worden aan de basis van de arm zodat hij zware objecten kan tillen.

# 2 Ontwerp

## 2.1 Blokschema

## 2.2 Componenten

## 2.3 BOM (Bill of Materials)

## 2.4 Schema

## 2.5 Board design

# 3 Realisatie

## 3.1 Bestukking

## 3.2 Programmatie

## 3.3 Motoren

# 4 Testen

## 4.1 Connecties

## 4.2 Veiligheid

## 4.3 Functionaliteit

## 4.4 Programmatie

## 4.5 Mechanische onderdelen

Conclusie

Literatuurlijst

[1] | „Domoticx,” [Online]. Available: https://ap.lc/deZqp. [Geopend 17 Maart 2023].
[2] | „Tinytronics,” [Online]. Available: https://ap.lc/eTqNZ. [Geopend 17 maart 2023].
[3] | „Tinytronics,” [Online]. Available: https://ap.lc/3loJv. [Geopend 17 maart 2023].
[4] | „Conrad,” [Online]. Available: https://ap.lc/pZaYL. [Geopend 17 maart 2023].
[5] | „Arduino,” [Online]. Available: https://ap.lc/OHA2n. [Geopend 18 maart 2023].
[6] | „Tinytronics,” [Online]. Available: https://ap.lc/gQWu6. [Geopend 18 maart 2023].
[7] | „Digikey,” [Online]. Available: https://ap.lc/i7Pd2. [Geopend 20 maart 2023].
[8] | Y. YAKIMOVA, „Europees parlement,” Europees parlement, 07 juni 2022. [Online]. Available: https://ap.lc/BxmRq. [Geopend 20 maart 2023].
[9] | „Mouser,” STMicroelectronics, 2021. [Online]. Available: https://ap.lc/08Oq4. [Geopend 20 maart 2023].
[10] | „Mchobby,” [Online]. Available: https://ap.lc/jClrO. [Geopend 17 maart 2023].
[11] | „Alldatasheet,” [Online]. Available: https://ap.lc/CW7Hs. [Geopend 17 maart 2023].
[12] | „Robotic arms,” [Online]. Available: https://ap.lc/cL01R. [Geopend 21 maart 2023].
[13] | R. Vaughn, „Machinedesign,” Machinedesign, 2 december 2013. [Online]. Available: https://ap.lc/Xp3Y1. [Geopend 21 maart 2023].
[14] | „Go to shoping,” [Online]. Available: https://ap.lc/ZoN4D. [Geopend 21 maart 2023].
[15] | M. Claussen, „Elektormagazine,” Elektormagazine, 12 juli 2022. [Online]. Available: https://ap.lc/lHw1e. [Geopend 21 maart 2023].
[16] | „Kuka,” Kuka, [Online]. Available: https://ap.lc/gyjYQ. [Geopend 21 maart 2023].
[17] | T. Nardi, „Hackaday,” Hackaday, 19 oktober 2020. [Online]. Available: https://ap.lc/UFSXb. [Geopend 21 maat 2023].

Bijlagenoverzicht

## Bijlage 1: Kopieën datasheets

## Bijlage 2: Logboek rapporteren

Lesweek 7: 13/02 – 19/02

Naam student | Paginanummers in rapport | Taak (bijv. schrijven klad, verbeteren, volledig herschrijven, nakijken, ...)
Lennert De Geeter | Vragenronde op school | Extra informatie vragen om een goed verslag op te stellen.
Roy De Volder | Vragenronde op school | Extra informatie vragen om een goed verslag op te stellen.
Jorik Van Dorpe | Vragenronde op school | Extra informatie vragen om een goed verslag op te stellen.
Lukas Verschraegen | Vragenronde op school | Extra informatie vragen om een goed verslag op te stellen.

Lesweek 8: 20/02 – 26/02

Naam student | Paginanummers in rapport | Taak (bijv. schrijven klad, verbeteren, volledig herschrijven, nakijken, ...)
Lennert De Geeter | Geen paginanummers (enkel brainstormen) | Brainstormen op papier/ digitaal op een tekentablet.
Roy De Volder | Geen paginanummers (enkel brainstormen) | Brainstormen op papier/ digitaal op een tekentablet.
Jorik Van Dorpe | Geen paginanummers (enkel brainstormen) | Brainstormen op papier/ digitaal op een tekentablet.
Lukas Verschraegen | Geen paginanummers (enkel brainstormen) | Brainstormen op papier/ digitaal op een tekentablet.

Lesweek 9: 27/02 - 5/03

Naam student | Paginanummers in rapport | Taak (bijv. schrijven klad, verbeteren, volledig herschrijven, nakijken, ...)
Lennert De Geeter | Pagina 7 | Inleiding
Roy De Volder | Pagina 1,3 | Hoofdblad opstellen
Jorik Van Dorpe | Pagina 1-11 | Controle
Lukas Verschraegen | Pagina 1-11 | Opstellen van het document volgens de regels uit het boek.

Lesweek 10: 5/03 - 12/03

Naam student | Paginanummers in rapport | Taak (bijv. schrijven klad, verbeteren, volledig herschrijven, nakijken, ...)
Lennert De Geeter | Pagina 23-25 | Het schrijven van een kladversie.
Roy De Volder | Pagina 26-28 | Het schrijven van een kladversie.
Jorik Van Dorpe | Pagina 22 | Het schrijven van een kladversie.
Lukas Verschraegen | Pagina 13-21 | Het schrijven van een kladversie.

Lesweek 11: 13/03 - 19/03

Naam student | Paginanummers in rapport | Taak (bijv. schrijven klad, verbeteren, volledig herschrijven, nakijken, ...)
Lennert De Geeter | Pagina 23-25 | Het herschrijven naar een correcte versie.
Roy De Volder | Pagina 26-28 | Het herschrijven naar een correcte versie.
Jorik Van Dorpe | Pagina 22 | Het herschrijven naar een correcte versie.
Lukas Verschraegen | Pagina 13-21 | Het herschrijven naar een correcte versie.

Lesweek 12: 20/03 - 26/03

Naam student | Paginanummers in rapport | Taak (bijv. schrijven klad, verbeteren, volledig herschrijven, nakijken, ...)
Lennert De Geeter | Pagina 13-19 | Nakijken tekst.
Roy De Volder | Pagina 7-11 / 30 | Controle van de lay-out.
Jorik Van Dorpe | Pagina 20-28 | Nakijken tekst.
Lukas Verschraegen | Pagina 7-11 / 30 | Opstellen van de lijsten volgens de regels uit het boek en verbeteren tekst.

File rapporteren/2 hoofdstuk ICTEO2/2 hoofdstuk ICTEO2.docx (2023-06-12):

Professionele bachelor Elektronica-ICT

Academiejaar: 2022 / 2023

# Het maken en sturen van een robotarm

Lectoren: Sabine Martens
Mario Wyns

Verslaggevers: Lennert De Geeter
Roy De Volder
Jorik Van Dorpe
Lukas Verschraegen

Klas: 3ELO

Professionele bachelor Elektronica-ICT

Academiejaar: 2022 / 2023

# Het maken en sturen van een robotarm

Lectoren: Sabine Martens
Mario Wyns

Verslaggevers: Lennert De Geeter
Roy De Volder
Jorik Van Dorpe
Lukas Verschraegen

Klas: 3ELO

Abstract

Inhoudsopgave

Figurenlijst

Tabellenlijst

Afkortingenlijst

Tabel 1: Afkortingenlijst

Afkorting | Betekenis
BOM | Bill of Materials
IC | Integrated circuit
DC | Direct current
PWM | Pulse-width modulation
MCU | Microcontroller unit
ESC | Electronic speed control
NEMA | National Electric Manufacturers' Association
pcb | Printed circuit board
IoT | Internet of Things
SoC | System-on-chip
SPI | Serial Peripheral Interface
I2C | Inter-Integrated Circuit
UART | Universal asynchronous receiver-transmitter
BLE | Bluetooth Low Energy
USB | Universal Serial Bus
LDO | Low-drop-out
TTL | Transistor-Transistor Logica
RMS | Root Mean Square
DIR | Direction
OTP | One-time programmable
SRAM | Static random-access memory
lcd | liquid crystal display
TMC | Trinamic
GPIO | General Purpose Input/ Output
elco | elektrolytische condensator

Begrippenlijst

Tabel 2: Begrippenlijst

Begrip | Verklaring
Brushless | Geen gebruik maken van fysieke contacten naar de commutator van de motor.
Flash | Flash is de verzamelnaam voor opslagsystemen waar data wordt opgeslagen op chips die hun informatie behouden nadat de voedingsspanning is weggehaald. Het is een vorm van niet-vluchtig geheugen dat in 1984 voor het eerst op de markt kwam.
SRAM | Static random-access memory is een geheugen waarvan de inhoud niet periodiek hoeft te worden geüpdatet. De opgeslagen data in een SRAM kunnen te allen tijde en in elke volgorde worden uitgelezen en wijzigen enkel als ze worden overschreven of als de IC spanningsloos wordt. Het is dus een vluchtig geheugen.
Pinout | Een pinout is een verwijzing naar de pinnen of contacten die een elektrisch apparaat of connector verbinden. Het beschrijft de functies van uitgezonden signalen en de circuit input/output (I/O) vereisten.
Royaltyvrij | Royaltyvrij is een term die wordt gebruikt om bepaalde soorten intellectuele eigendom te beschrijven zonder royalty's te betalen. Eigenaars van intellectuele eigendom moeten dit label specifiek op hun inhoud toepassen, zodat iedereen het op dezelfde manier kan gebruiken.
Beheersmaatregelen | Beheersmaatregelen zijn de maatregelen die worden genomen om de risico's waaraan ondernemingen blootstaan te beheersen.
Consciëntie | Nauwkeurigheid.
SCARA | Selective Compliance Articulated Robot Arm
Interferentie | Interferentie is de samen- of tegenwerking van verscheidene golven op dezelfde tijd en plaats.

Inleiding

In dit project wordt een prototype van een robotarm ontworpen en ontwikkeld. De arm moet met toegankelijke hardware en machines kunnen worden vervaardigd kunnen. De robotarm wordt ontworpen binnen een industriële omgeving waar hij repetitieve taken precies zal moeten uitvoeren.

In een eerste hoofdstuk wordt onderzoek gedaan naar de verschillende mogelijkheden van de arm. Die kan namelijk mechanisch uit heel wat verschillende ontwerpstrategieën bestaan. Ook kan afhankelijk van de toepassing en de grijpfunctionaliteit andere tooling nodig zijn. De robotarm wordt logischerwijze gestuurd door motoren, ook hier zijn weer een aantal mogelijkheden met voor- en nadelen. De robotarm is een prototype voor in een industriële omgeving, ook veiligheid is dus een aandachtspunt.

Eens de basiseigenschappen in het onderzoek zijn uitgeklaard, kan al deze kennis in het ontwerp worden overgenomen. Dat is dan ook het volgende hoofdstuk van dit onderzoek en omvat zowel een mechanisch als elektronisch ontwerp. Delen zoals een blokschema, componenten, Bill of Materials en elektronische schema’s, alsook een finaal mechanisch ontwerp worden in dit tweede hoofdstuk besproken.

Eens alle ontwerpen en onderzoeken zijn uitgevoerd, kan er worden overgegaan tot de realisatie van de arm. In het derde hoofdstuk wordt de bestukking van de pcb

besproken en de programmatie ervan. Ook het 3D-printen van de arm en zijn assemblageproces komen hier aan bod.

Wanneer de robotarm tot slot dan volledig geassembleerd is, kan de testfase worden ingezet. In dit vierde hoofdstuk worden functionaliteit en veiligheid extra onder de loep genomen en eveneens het oplossen van problemen met mechanische onderdelen en programmatie.

Via een experimentele onderzoeksmethode wordt dit project en dossier opgebouwd. De belangrijkste bronnen zijn datasheets van de componenten en diverse online bronnen en ontwerpen.

# 1 Onderzoek

Om vlot van start te gaan met het project is het belangrijk om voorkennis te hebben van de onderdelen van een robotarm.

In dit hoofdstuk worden verschillende onderdelen vergeleken die noodzakelijk zijn om een robotarm te laten functioneren. De focus ligt vooral op de realiseerbaarheid en het gebruiksgemak van verschillende producten. Vooraleer een ontwerp van toepassing is, is vergelijken van producten noodzakelijk om te weten wat haalbaar is. Kosten en gebruiksgemak zijn hierbij uiteraard belangrijk.

De motoren, sensoren, het mechanische deel van de robotarm, de veiligheid en tot slot het opzetstuk van de robotarm zijn de belangrijkste onderdelen van dit project. Dit is de reden waarom er naar elk onderdeel onderzoek zal gebeuren. Om verschillende materialen te verplaatsen zijn immers andere en eventueel nauwkeurigere opzetstukken nodig. Hierdoor wordt het belang van de vervangbaarheid van een opzetstuk benadrukt.

## 1.1 Motoren

De hoofdzaak, en tevens de belangrijkste onderdelen van een robotarm zijn de motoren. De kern van een motor bestaat uit een koperen spoel met een massadichtheid van 8,96 kg/m³. Met als gevolg dat koper zwaar is, wat op zijn beurt de belangrijkheid van de keuze van motor weergeeft. [1]

Eerst wordt aan de basis geopteerd om een motor van 300 à 400 gram te gebruiken. Vervolgens gaat op het uiteinde van de robotarm de keuze naar een motor van 50 à 60 gram. Ten slotte is het doel dat het geheel van de motoren nog steeds krachtig genoeg is om 250 tot 500 gram op te tillen.

Bovendien is de vloeiende beweging van een motor belangrijk. Uiteraard is dit afhankelijk van de sensoren waarmee de motor wordt aangestuurd. Vandaar het gebruik van motoren die gemakkelijk compatibel zijn met een IC. Om de kracht in de motor te behouden, wordt onderzocht of er interne tandwielen zijn geplaatst.

Naast de vooraf besproken aspecten speelt ook de kostprijs - die varieert naargelang de grootte van de motor - een grote rol. Hoe groter de motor, hoe hoger de prijs is, want hoe groter de motor, hoe meer koper er wordt gebruikt, en koper is duur. Alhoewel energiezuinigheid belangrijk is, is een motor dit meestal niet.

Er bestaan verschillende motoren zoals: stappenmotoren, servomotoren, DC-motoren en brushless DC-motoren. De vergelijking en de uitleg van de meest voorkomende motoren in de elektronica staan in Tabel 3Tabel 3: Vergelijking van motoren [2] [3]. De vergeleken motoren zijn geselecteerd op basis van populariteit en kracht.

### 1.1.1 Stappenmotor

Als er gekeken wordt naar kracht en populariteit, dan wordt er vaak gebruik gemaakt van een NEMA 17-motor, de motor is vooral populair in toepassingen met de 3D-printer [2].

### 1.1.2 Servomotor

Bij een servomotor is kracht een grote factor, een motor die 25 kg kan heffen is dus de beste keuze. De td-8125mg is een veel gebruikte optie en is hier de beste mogelijkheid [3].

### 1.1.3 DC-motoren

Voor DC-motoren wordt de term “transmissiemotor” gebruikt. Deze term is te verklaren omdat er bij dit type motor gebruik wordt gemaakt van een tandwieloverbrenging. [4]

### 1.1.4 Brushless DC-motoren

Aangezien de brushless DC-motoren van oorsprong weinig gewicht kunnen dragen, is de populariteit van belang. Dronemotoren, zoals de Pichlermotor, zijn de meest gebruikte in hun soort [5].

De conclusie die uit Tabel 3 kan worden getrokken, is dat er in dit project een combinatie van stappenmotoren en servomotoren wordt gebruikt. De brushless DC-motor en de DC-motor hebben allebei een continue beweging, wat niet ideaal is, en ze worden om die reden niet in dit project gebruikt.

Tabel 3: Vergelijking van motoren [2] [3] [2] [3]

| Stappenmotoren [2] | Servomotoren [3] | DC-motoren [4] | Brushless DC-motoren [5]
Beweging | Een stappenmotor kan verschillende posities aannemen. Er is een vloeiende beweging om van de ene positie naar de andere te gaan. De verandering gebeurt heel snel en precies. | Een servomotor heeft een vloeiende beweging bij het verdraaien, maar is niet altijd even precies doordat sommige motoren plastic tandwielen hebben. Het voorbeeld is daarom met metalen tandwielen. | De vloeiende beweging van een DC-motor draait constant in eenzelfde richting. Voor de robotarm is de DC-motor niet geschikt aangezien er een positie moet worden bepaald. | Een brushless DC-motor is een motor die heel vloeiend draait, maar hij heeft ook een continue beweging zoals de normale DC-motor. Er is ook een speciale sturing nodig om controle te krijgen over de snelheid.
Gewicht motor | 280 g | 62 g | 200 g | 29 g
Hefkracht | 4,0 kg/cm | 25 kg/cm | 75 kg/cm | 730 g/cm
Kostprijs | € 11 | € 11,5 | € 12 | € 27,99
Tandwielen | Er zijn geen ingebouwde tandwielen aanwezig. | De motor in het voorbeeld heeft ingebouwde, metalen en robuuste tandwielen om aan een groot hefvermogen te komen. | De motor in het voorbeeld heeft ingebouwde, metalen en robuuste tandwielen om aan een groot hefvermogen te komen. | Er zijn geen ingebouwde tandwielen aanwezig.
Draaihoek | Er is een staphoek van 1,8° per stap. | 0-180° aangestuurd met een PWM-signaal. | Een DC-motor heeft altijd een continue draaihoek, en is dus niet instelbaar. | Een brushless DC-motor heeft altijd een continue draaihoek, en is dus niet instelbaar.
Stroom | 1,7 A | 3,4 A | 200 mA | 23 A
Aanstuurbaarheid | Aangezien er meerdere spoelen worden gebruikt in de motor is er een bepaalde IC nodig om ze aan te sturen. | De servomotor heeft de mogelijkheid om via PWM te worden aangestuurd. Dit is gemakkelijk omdat bijna elke MCU dit signaal kan genereren. | Deze motor kan worden aangestuurd door voeding op de motor te zetten, dit werkt zonder enig stuursignaal. | Om aan te sturen heeft de brushless DC-motor een ESC nodig.
Aansluitbaarheid | Deze motor heeft een dikke en stevige as van 5 mm diameter om iets op aan te sluiten. Een veel gebruikte motor is een NEMA 17-motor met standaard montagepunten. | De motor heeft een metalen as met ribbels om betere grip te krijgen en een hol center waar een schroef kan worden ingedraaid. De aansluiting is dus heel sterk en stevig. Een nadeel is dat de diameter van de as redelijk klein is. Er zijn twee montagepunten aanwezig. | De aansluitbaarheid bij deze DC-motor is super, hij heeft een D-vormige as voor ultieme krachtoverbrenging. De asdiameter is 6 mm en de motor zelf heeft geen montagepunten. | De motor kan goed aan onderdelen worden gekoppeld, doordat hij een stevige metalen as heeft met een diameter van 15 mm. Hierop zit nog een bevestigingsstuk dat kan worden vastgeschroefd. De motor heeft vier montagepunten.

## 1.2 Sensoren

Sensoren zijn van groot belang bij een robotarm. Vooraleer de sensoren iets kunnen lezen of sturen, moet er een microcontroller worden gezocht. De MCU stelt het brein van de pcb voor en is extreem belangrijk.

Er bestaan verschillende modellen microcontrollers. Aangezien een wificonnectie belangrijk is om bijvoorbeeld data te sturen naar een website, zijn er enkele microcontrollers die gebruik maken van ingebouwde antennes. Ze worden gebruikt bij IoT-toepassingen (Internet of Things).

Er wordt een vergelijking gemaakt tussen de twee populairste MCU’s van de grootspelers op de markt, namelijk Arduino met “Arduino mkr wifi 1010” Figuur 1 [6] en Espressif met ”ESP32” Figuur 2 [7]. Tabel 4

Aangezien de ESP-boards open source zijn, zijn er ook andere fabrikanten die gelijkaardige system on a chip (SoC) microcontrollers verkopen.

De ESP-boards kunnen zowel voor professionele als amateuristische toepassingen worden gebruikt. De boards zijn open source en op die manier is het gemakkelijk om te achterhalen hoe ze kunnen worden geprogrammeerd.

ESP32 WiFi and Bluetooth Board - CP2102

Figuur 1: Arduino mkr wifi 1010 [6]

Figuur 2: ESP32 [7]

Tabel 4: Microcontrollers vergelijken [6] [7]

Fabrikant | Arduino [6] | | Espressif [7]
Product | Mkr wifi 1010 | | ESP32
Chip | ATSAMD21 | | ESP32-WROOM-32D
Geheugen | FLASH: 256 kB | SRAM: 32 kB | FLASH: 4 MB | SRAM: 520 kB
Interface | SPI/ I2C/ UART | | SPI/ I2C/ UART
Wifi | Ja | | Ja
BLE | Neen | | Ja
Voltage | 5 V-input | 3,3 V-output | 5 V-input | 3,3 V-output
Pinout | Digitaal/ analoog/ PWM | | Digitaal/ analoog/ PWM
Afmetingen | 61,5 mm x 25 mm | | 52 mm x 28 mm
Prijs | € 33,50 | | € 9,50

Wat direct opvalt bij de vergelijking is de prijs, de Arduinomicrocontroller is veel duurder. De rest van de eigenschappen is zo goed als gelijk. Bij de variant van Espressif is het geheugen beter én is er de mogelijkheid om voor die goedkopere prijs zelfs BLE te hebben.

Op basis van de beschikbare informatie is Espressif de beste optie voor MCU’s. De ESP32 is een heel goed ondersteunde microcontroller om de nodige doeleinden waar te maken. Dit hoeft niet precies de ESP-WROOM-32 te zijn, maar kan ook een variant zijn binnen deze familie, aangezien de meeste eigenschappen worden gedeeld. Tabel 4

Nu de chip gevonden is, is het belangrijk om te weten welke sensoren compatibel zijn met deze MCU’s.

Er wordt eerst gekeken hoe een ESP32 van spanning en van stroom wordt voorzien als er alleen met de chip wordt gewerkt [8]. Een afbeelding van de chip Figuur 3: ESP32-WROOM-32D chip zonder pcb [8]te zien.

Figuur 3: ESP32-WROOM-32D chip zonder pcb [8]

### 1.2.1 Voeding

Volgens een bron van het Europees Parlement [9] wordt er vroeg of laat voor elk nieuw elektrisch apparaat op de handelsmarkt gebruik gemaakt van USB-C. Dit zou vanaf de herfstperiode van 2024 langzaam worden ingeburgerd.

Dit is een goede reden om USB-C te implementeren in het project. De connector heeft als eigenschap dat hij gebruiksvriendelijk is. Het maakt niet uit in welke richting de kabel wordt aangesloten, communicatie en voeding met het apparaat is er direct via de 24 pins-connector. Het grote voordeel van USB-C is dat er een hogere datatransmissiesnelheid is en een hogere stroomvoorziening van 100 W bij 20 V en 5 A. Een voorstelling van zo een connector Figuur 4.

What is USB C? USB C Plug & Receptacle Pinouts | Arrow.com | Arrow.com

Figuur 4: USB-C-pinout [9]

De voorstelling hierboven (Figuur 4), geeft de pinnen weer voor elk mogelijk protocol. Er zijn verschillende protocollen zoals Thunderbolt, Displayport, HDMI en USB die USB-C ondersteunen. Belangrijk voor de communicatie met de ESP-chip is het USB-protocol.

Om de ESP te voeden, is het belangrijk dat die de juiste spanning krijgt. De chip wordt gevoed met een spanning van 3,3 V en dit wordt met een low-drop-outregulator (LDO) verkregen.

Dit is een lineaire DC-spanningsregelaar die de uitgangsspanning stabiel kan regelen op 3,3 V.

Het systeem werkt volgens het principe met potentiaalverschil tussen input en output, de ingang moet altijd hoger zijn dan de uitgang. Het energieverlies tussen deze twee spanningen wordt omgezet in warmte.

Er is geen verklaring voor de specifieke waarde van de condensatoren die rond een LDO staan (Figuur 5). De elektrolytische condensatoren dienen in een schakeling als spanningsbuffer. Er is bijgevolg nog steeds een kleine spanning aanwezig als de algemene spanningsbron plots wegvalt in het circuit.

Keramische condensatoren zijn meestal heel laag van capaciteit en worden bij een LDO gebruikt als ontkoppelcondensatoren. Die dienen om ruis te filteren dat aanwezig is in een schakeling. [10]


Figuur 5: Typische applicatie LDO [10]

### 1.2.2 Communicatie

Om te communiceren met een ESP-32 moet er een aparte chip worden gebruikt. Eén van de veel gebruikte mogelijkheden is de CP2102. Uit de USB-C-poort komt een protocol dat USB heet, maar dit verstaat de ESP-32 niet. Wat de ESP wel verstaat is het UART-protocol. Dit is de reden waarom wordt gedacht aan de veel gebruikte CP2102, het is namelijk een USB naar TTL Serial UART-convertor.

TTL staat voor Transistor-Transistor Logica en heeft een spanningsniveau van 0 tot 5 V. Het is een chip op basis van transistoren.

De CP2102 biedt een complete plug-and-play-interface-oplossing met royaltyvrije stuurprogramma's. De chip is USB 2.0-compatibel, wat zorgt voor snelle communicatie.

### 1.2.3 Programmatiecircuit

Er is een resetknop en een flashknop (of bootknop) vereist om een programma op de microcontroller te laden. De functie van de resetknop is om de enablepin van de MCU naar een ground te trekken omdat de enablepin standaard op een hoog niveau staat. Als dit gebeurt, dan wijkt de chip af van zijn standaardprogramma, wordt het onderbroken en ook gereset.

Om programma’s in te laden, kan er gebruik worden gemaakt van een transistornetwerk om automatisch in te laden. Hiervoor is geen knop meer nodig. Als dit netwerk niet aanwezig is, wordt er tijdens het inladen van het programma op de flashknop gedrukt.

### 1.2.4 Sensor voor het aansturen van de stappenmotor

TMC2208 is een ultrastille tweefasige stappenmotordriverchip [11]. Het stuurt de motoren aan door full- en microstepping Figuur 6. TRINAMIC's geavanceerde stealthChop2 technologie zorgt voor een geruisloze werking, maximale efficiëntie en het beste motorkoppel. De snelle stroomregeling en de optionele combinatie met spreadCycle zorgen voor een zeer dynamische beweging.

Variable rate based microstepping of stepper motor using MATLAB GUI | Semantic Scholar

Figuur 6: Full-step vs. micro-step [12]

De bedoeling van microstepping is het omzetten van de blokgolf die de motor aanstuurt naar een sinusgolf. Een perfecte sinusgolf wordt nooit behaald, maar de TMC2208 komt, in vergelijking met de A4988 en andere chips, er het dichtste bij omdat het gebruik maakt van 1/256-microstepping. Zo worden de stappen zeer klein en worden er minimale trillingen gegenereerd, waardoor deze chip de motor zeer stil doet draaien.

Zonder microstepping maakte bijvoorbeeld een 4-stappenmotor vier stappen per volledige aswenteling (dus 90° per stap). Door gebruik te maken van een 1/256-microstepping worden de motorspoelen zo aangestuurd dat er 4*256=1024 stappen nodig zijn om een volledige omwenteling te maken (dus 0,3515625° per microstap).

Eigenschappen [13]:

- Aandrijfcapaciteit tot 1,2 A (RMS) continue spoelstroom - 2 A-piek
- STEP/DIR-interface met 2, 4, 8, 16 of 32 microstep-pininstelling
- 256 microstappen door microPlyer™-interpolatie
- StealthChop2 voor stille werking en vloeiende bewegingen (standaardinstelling)
- SpreadCycle zeer dynamische motorbesturing chopper (schakelbaar via UART)
- Voedingsspanning motor: 5,5 tot 36 V
- Logische voedingsspanning: 3,3 tot 5 V
- Automatische stand-by stroomreductie (optie)
- Passief remmen en vrijloop
- Single Wire UART & OTP voor geavanceerde configuratie-instellingen
- Geïntegreerde pulsgenerator voor zelfstandige beweging

Een andere keuze om de motoren aan te sturen is de A4988 microstepping stappenmotordriver. Het voordeel van deze chip is dat hij een beetje goedkoper is. Het nadeel en de reden waarom deze chip niet wordt gebruikt, is dat de motoren veel meer lawaai maken.

## 1.3 Mechanica

In een vorig hoofdstuk werden de verschillende types motoren al besproken. Zoals werd bekeken heeft ieder type motor een verschillende draagkracht, en is die dus ook beter toepasbaar op verschillende punten.

Bij industriële armen wordt voor de scharnierpunten gebruik gemaakt van stappenmotoren en servomotoren. Afhankelijk van het type motor is een andere mechanische ontwerpstrategie nodig. Het prototype, besproken in dit dossier, wordt uitgewerkt met een 3D-printer, ook dat is een belangrijk punt om rekening mee te houden. De verschillende mogelijkheden met deze eigenschappen kunnen worden opgedeeld in drie groepen.
Deze groepen bestaan uit een cartesische, een articulated en een SCARA-robotarm, deze is te zien op de figuur hieronder. Figuur 7 [14]


Figuur 7: Verschillende types robotarmen [14]

### 1.3.1 Cartesische robotarm

De cartesische robot lijkt het meeste op een klassieke CNC-machine of 3D-printer. Cartesische of lineaire robots werken op drie assen: X,Y en Z. Deze drie assen maken het mogelijk om in drie dimensies te bewegen: horizontaal (X- en Y-as) en verticaal (Z-as). Dit type robot is erg flexibel dankzij de specifieke opbouw. Zo kan die snel en eenvoudig worden aangepast, afhankelijk van de toepassing. Deze hoge flexibiliteit is te danken aan de typerende aluminiumprofielen waaruit de robot is opgebouwd. Deze profielen zijn internationaal verkrijgbaar in verschillende lengtes en breedtes en laten zich erg makkelijk bewerken. Hierdoor kunnen lagers, geleiders en andere componenten makkelijk en snel worden gemonteerd. Door deze standaardprofielen kan ook de prijs van een cartesisch systeem erg aantrekkelijk zijn. Figuur 8 [15] [16]

Figuur 8: Cartesische robotarm en de aluminium profielen [16] [15]

Een mogelijke toepassing van dit ontwerp is het open source LumenPnP-project door Opulo. Figuur 9 [17]

Figuur 9: LumenPnP cartesische robotarm [17]

Deze machine maakt het voor iedereen mogelijk printplaten op één niveau met hoge precisie te bestukken. De machine beweegt op de drie assen in rechte lijnen, een toepassing waar de cartesische robot uiterst geschikt voor is.

Zoals al eerder vermeld wordt het volledige werkgebied afgebakend. Dit is een nadeel voor de robot die in dit onderzoek wordt gemaakt, aangezien bewegingsvrijheid een belangrijk punt is.

### 1.3.2 Articulated robotarm

Een derde type is de articulated of vrijdraaiende robot. Dit type robot lijkt het best op een menselijke arm met alle bijbehorende voordelen. Deze robotarm wordt gemonteerd op een draaiende basis. Met een basisaantal motoren kan de volledige 3D-ruimte rondom de arm worden bereikt. Naarmate meer motoren en assen worden toegevoegd, wordt de toegankelijkheid van dit gebied nog verbeterd. Dit type robot kent een wijde inzetbaarheid in de industrie; van taken zoals lassen en materialen verplaatsen tot volledige assemblage en inpakken. Figuur 10 [18]


Figuur 10: Lasrobot [18] Figuur 11: Assemblagerobot [18]

Eén van de voordelen van dit ontwerp is de centrale basis waar de hele arm op draait. In dit onderzoek brengt dit een belangrijk punt met zich mee, namelijk dat het volledige gewicht op één centrale motor en as terechtkomt. De andere motoren werken wel mee aan de beweging, op voorwaarde dat de onderste as die kan ondersteunen.

Om dit allemaal mogelijk te maken, zijn overbrengingen op de motoren erg belangrijk.

### 1.3.3 SCARA-robotarm

Het SCARA-ontwerp heeft net zoals de cartesische robot drie assen waarop die beweegt. Het verschil tussen beide is de manier waarop wordt bewogen. Het cartesische ontwerp doet dat telkens in een hoek van 90°, terwijl een SCARA-robot om zijn eigen as kan draaien. Dat maakt dit ontwerp uiterst geschikt voor het stapelen van dozen of voor assemblage. Figuur 12 [15]

Figuur 12: Scara-robotarm [15]

Voor dit ontwerp zijn verschillende opensourcetoepassingen beschikbaar. Bijvoorbeeld dit type door PyBot. [19]

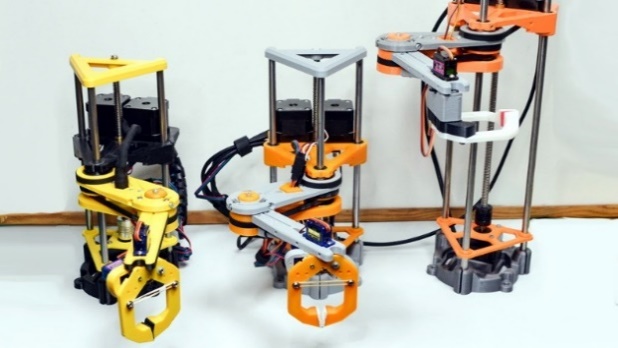
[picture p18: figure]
PyBot Is A 3D Printed SCARA Arm For The Masses | Hackaday

Figuur 13: Uitgewerkt versie PyBot [19] Figuur 14: 3D-Assenstelsel [19]

Het is opnieuw volledig uitgewerkt op een 3D-printer met standaardcomponenten erin verwerkt. Dit type geeft door zijn enkele roterende basis een beter beeld van de toepassing in dit onderzoek. Hij is gelimiteerd in de bewegingen die worden gemaakt. Zo is iedere beweging in de Z-richting of hoogte afhankelijk van één motor. Figuur 13/ 14

## 1.4 Veiligheid

Bij het ontwerpen en realiseren van een robotarm zijn verschillende aspecten van veiligheid van belang. Het uitvoeren van een goede risicoanalyse is cruciaal om mogelijke gevaren te identificeren. Deze gevaren zouden zich kunnen voordoen tijdens het gebruik van de robotarm. Het is daarbij van belang om potentiële gevaren voor zowel de bediener als andere personen in de omgeving van de robotarm te evalueren.

Stap één van de risicoanalyse omvat de identificatie van mogelijke gevaren, zoals snelle bewegingen van de robotarm die letsels kunnen veroorzaken, hoge temperaturen bij het gebruik van de robotarm, blootstelling aan elektrische stroom en mogelijke botsingen met personen of objecten in de buurt.

Stap twee van de risicoanalyse omvat de evaluatie van de waarschijnlijkheid dat de gevaren zich zullen voordoen en de mogelijke ernst van de gevolgen als ze zich voordoen. Op basis hiervan kan worden bepaald welke risico’s prioriteit hebben bij het nemen van beheersmaatregelen.

Stap drie van de risicoanalyse omvat het identificeren van beheersmaatregelen om de risico’s te verminderen of te elimineren. Dit kan bijvoorbeeld worden bereikt door het installeren van fysieke barrières rondom de robotarm of door gebruik te maken van sensoren die de robotarm kunnen stoppen wanneer een persoon in de buurt komt. Het is daarbij van belang om noodstoppen te installeren die de robotarm onmiddellijk stoppen wanneer er een onverwachte situatie ontstaat. Verder moeten alle gebruikers van de robotarm getraind zijn om veilig gebruik te maken van de robotarm en eveneens van de bijhorende apparatuur. Ook regelmatig onderhoud en inspectie zijn belangrijk om preventief te kunnen handelen.

Door rekening te houden met deze factoren en andere belangrijke veiligheidsaspecten, kunnen ontwerpers en gebruikers ervoor zorgen dat de robotarm veilig en efficiënt werkt. [20]

## 1.5 Opzetstuk

Eén van de belangrijkste aspecten bij het maken van een robotarm is het ontwerpen van de opzetstukken. Een opzetstuk is het deel van de robotarm dat in contact komt met het object dat wordt verplaatst of bewerkt. Het type opzetstuk dat wordt gebruikt, hangt af van de toepassing en het gewenste resultaat.


Eén van de meest voorkomende opzetstukken voor een robotarm is de grijper. Dit opzetstuk wordt gebruikt om objecten vast te pakken en te verplaatsen. Er zijn verschillende soorten grijpers, zoals parallelle grijpers, hoekgrijpers en pneumatische grijpers. Parallelle grijpers worden vaak gebruikt bij industriële toepassingen, zoals het assembleren van producten, het verpakken van goederen of het laden en lossen van vrachtwagens. Ze zijn ook populair in laboratoriumomgevingen en in de gezondheidszorg voor het hanteren van delicate en gevoelige objecten. Over het algemeen bieden parallelle grijpers een betrouwbare en efficiënte manier om objecten vast te pakken en te hanteren met behulp van een robotarm. Figuur 15

Figuur 15: Parallelle grijper [20]

Hoekgrijpers zijn een ander type grijper dat vaak wordt gebruikt. Zoals de naam al aangeeft, zijn hoekgrijpers ontworpen om objecten vast te pakken en vast te houden met behulp van een set vingers die in een hoek zijn gepositioneerd ten opzichte van elkaar. Dit type grijper wordt gebruikt in toepassingen waarbij het vast te pakken voorwerp niet plat of rechthoekig is, maar een onregelmatige vorm heeft. Pneumatische grijpers worden voornamelijk gebruikt voor het hanteren van delicate objecten zoals objecten die gemaakt zijn van glas of breekbaar materiaal. Figuur 16

Figuur 16: Pneumatische hoek-grijper [21]

Een ander type opzetstuk is een lasersnijder. Dit opzetstuk gebruikt lasers om materialen te snijden. Het is vooral handig bij industriële toepassingen waar precisie en snelheid van belang zijn, zoals bij het snijden van metaalplaten.

Schuurmachines zijn een andere soort veelvoorkomende types van opzetstukken voor een robotarm. Ze worden gebruikt om materialen te schuren en glad te maken. Dit type opzetstuk wordt het meest gebruikt in de automobiel- en meubelindustrie.

Een magnetisch opzetstuk wordt gebruikt om metalen voorwerpen op te tillen en te verplaatsen. Dit type opzetstuk is handig voor het hanteren van zware of gevaarlijke metalen voorwerpen. Dit kan bijvoorbeeld van pas komen in een fabriek waar zware metalen onderdelen worden geproduceerd. Het gebruik van een magnetisch opzetstuk kan de efficiëntie en productiviteit van de robotarm verbeteren. Het kan immers snel en gemakkelijk objecten oppakken en verplaatsen zonder dat er veel aanpassingen nodig zijn. Bovendien verkleint de kans op ongevallen door vallende voorwerpen omdat ze beter vasthangen aan de robotarm.

Het is ook mogelijk om camerasystemen te gebruiken als opzetstuk. Dit type opzetstuk wordt gebruik om beelden vast te leggen en te analyseren. Het wordt vaak gebruikt in de industrie voor kwaliteitscontrole, inspectie en robotica-onderzoek. Het camerasysteem kan er in combinatie met andere types opzetstukken voor zorgen dat bijvoorbeeld delicate voorwerpen beter gegrepen kunnen worden omdat er voorziening is van een beter beeld.

Men kan een robotarm ook uitrusten met een boormachine als opzetstuk om gaten te maken in materialen. Dit soort opzetstuk is ideaal voor situaties waarbij precisie, consciëntie en herhaalbaarheid van cruciaal belang zijn. Een robotarm met een boormachineopzetstuk kan ook worden gebruikt om schroeven te draaien in onderdelen die al voorzien zijn van schroefgaten. Dit vermindert de noodzaak van menselijke arbeid en verbetert de efficiëntie van het productieproces. Naast boren en schroeven kan de robotarm gebruik maken van een boormachineopzetstuk om een bepaald patroon in een materiaal te frezen.

De keuze in gebruik van het soort opzetstuk is belangrijk in het designproces van de robotarm. Hij kan op die manier volledig naar wens worden gemaakt en er kan eventueel extra gewicht worden toegevoegd aan de basis van de arm zodat hij objecten van 250 tot 500 gram kan tillen.

# 2 Ontwerp

## 2.1 Blokschema

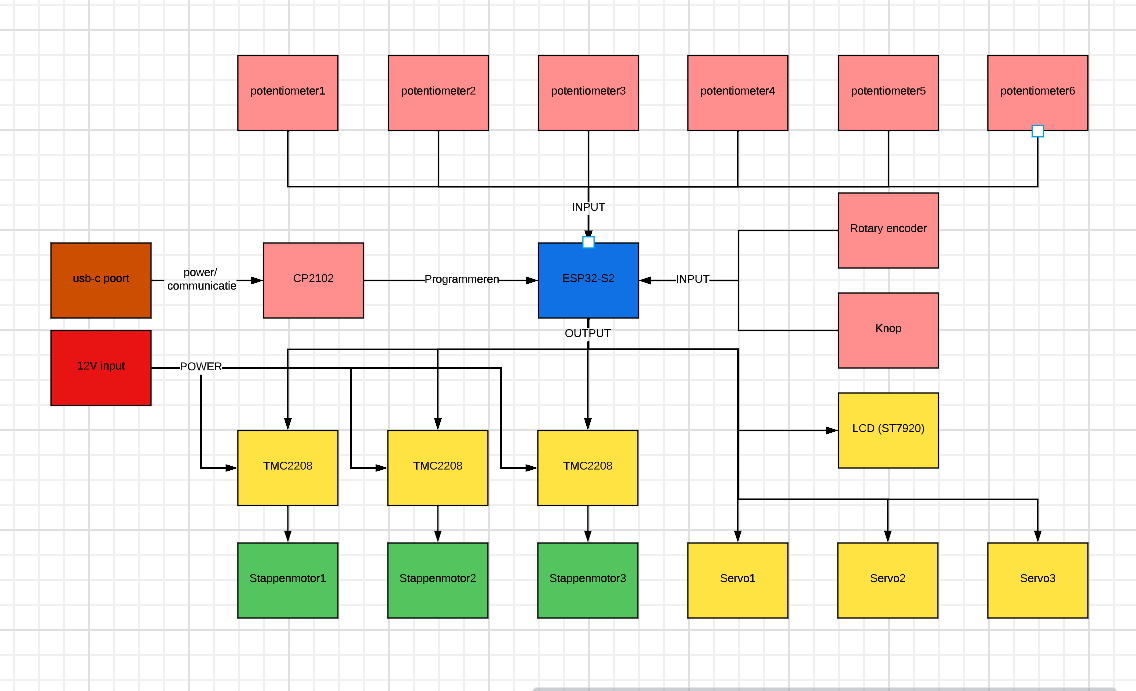
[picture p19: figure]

Figuur 17: Blokschema

Dit blokschema zorgt ervoor dat er een duidelijk overzicht is van alle belangrijke componenten die worden gebruikt in het project. Wat opvalt, is dat er verbindingen worden gemaakt tussen de blokken. De pijlen geven de richting aan waarin de communicatie loopt.

De functie van de pijlen – input/ output, programmeren, power – staat erbij vermeld.

De ESP32-S2 is hier duidelijk het centrale communicatiepunt. Dit is logisch omdat deze chip het brein van het systeem vormt. De chip stuurt signalen zoals PWM/ I2C/ SPI uit via de outputs en kan analoge ingangen uitlezen van bijvoorbeeld een potentiometer.

Het blokschema heeft een kleurencode, hierdoor wordt in één oogopslag duidelijk hoe de werking en opstelling van het bord is.

De legende is als volgt voor Figuur 17:

- Roze: alle inputsystemen zoals de communicatie voor de chip en de analoge ingangen.
- Geel: alle outputs naar drivers/ servomotoren en een lcd.
- Groen: de stappenmotoren die afhankelijk zijn van een driver zoals de TMC2208
- Blauw: het brein van het systeem, de ESP32-S2.
- Rood: voeding naar het systeem.

Het blokschema is nuttig, aangezien dit een vertrekpunt is voor een elektrisch schema.

Het elektrisch schema wordt besproken in hoofdstuk 2.4.

## 2.2 Componenten

Alle componenten kunnen individueel worden gerealiseerd. Dit is de reden waarom elk belangrijk stuk van het schema eerst apart wordt besproken. Uiteraard wordt het belangrijkste stuk eerst besproken, namelijk de ESP32-S2.

### 2.2.1 ESP32-S2

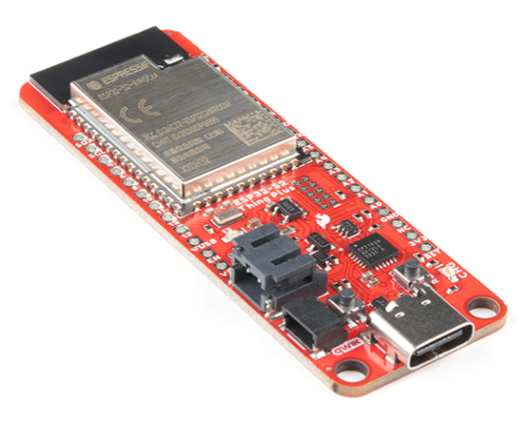
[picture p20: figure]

Figuur 18: SparkFun Thing Plus - ESP32-S2 WROOM [21] Figuur 19: ESP32-S2 chip [22]

Om van start te gaan met de ESP32-S2 is het belangrijk de eigenschappen te bekijken van de chip. De meest belangrijke eigenschappen zijn USB-C, wifi, en meer GPIO-pinnen dan een standaard ESP32.
Het gebruik van de ESP32-S2 is perfect in dit project, de bluetoothfunctie van deze chip is ingewisseld voor extra GPIO-pinnen. Dit wil zeggen dat deze microcontroller beschikt over 43 GPIO-pinnen die in verschillende functies kunnen worden geconfigureerd. [22]

Het Sparkfunboard zorgt voor een goede start en basisdocumentatie om een schema op te bouwen. [21]

Bij deze microcontroller is vooral belangrijk dat de wifiantenne volledig vrij moet zijn en geen interferentie mag krijgen door draden of baantjes op de pcb. De ESP heeft een standaard USB-connectie ingebouwd, welke vrij moet blijven om een externe verbinding mogelijk te maken. Figuur 18/ 19

### 2.2.2 TMC2208

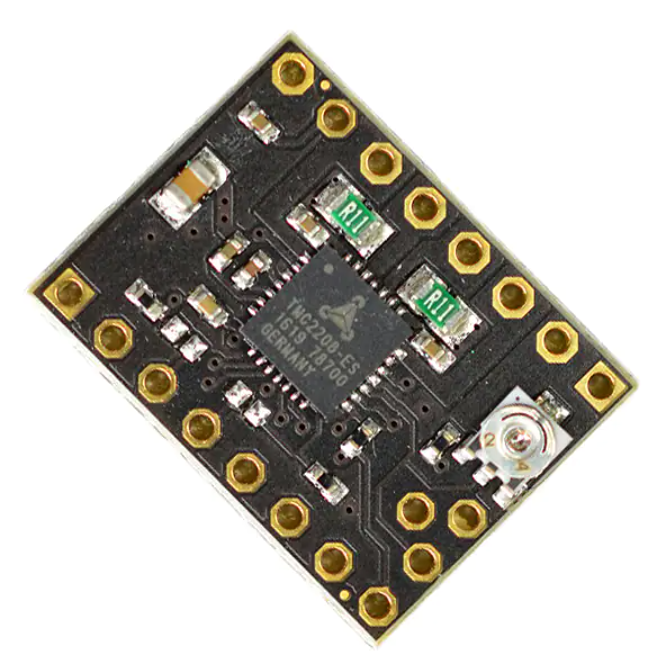
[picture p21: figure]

Figuur 20: Digikey TMC2208 board [23]

Bij het ontwerpen van deze pcb is rekening gehouden met de stroom die de TMC moet krijgen. Aangezien deze driver een motor aanstuurt, levert de TMC een maximale stroom van 1,2 A en daarom is de baandikte bij de pcb berekend zoals in hoofdstuk 2.5 wordt besproken. De stroom is instelbaar met de potentiometer die aanwezig is per driver op de pcb. Op de foto staat de potentiometer – het metalen object gemonteerd op de pcb - uiterst rechts.

Op zijn website stelt de fabrikant veel informatie ter beschikking. [23] Digikey heeft veel ervaring bij het ontwikkelen van een prototype van deze module. Momenteel bestaat versie twintig van het elektrisch schema en daarom is er gebruik van gemaakt. Figuur 20

Bij het implementeren op een eigen printplaat moet rekening worden gehouden met enkele factoren. Aangezien de chip heel warm kan worden door het stroomverbruik, moet er aandacht worden besteed aan een goede koeling en eventueel een koelvin.

### 2.2.3 CP2102

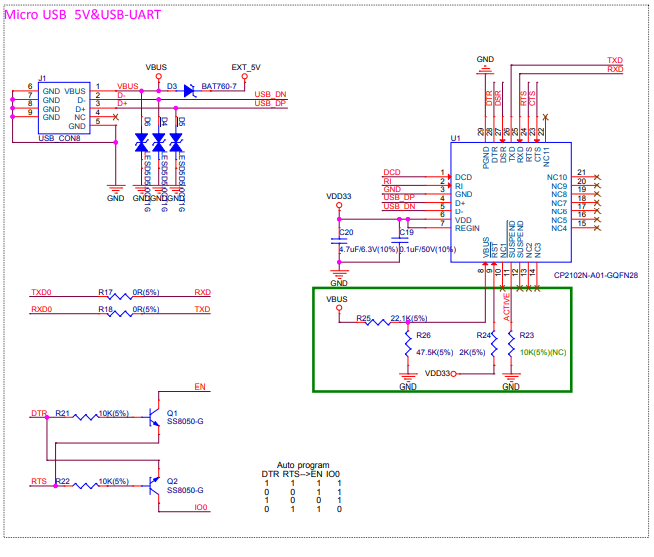
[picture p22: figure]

Figuur 21: CP2102 schema [24]

De CP2102 is een veel gebruikte chip om te communiceren van USB naar UART. Door gebruik te maken van deze chip, kan er seriële communicatie worden gevormd. Het debuggen wordt op deze manier gemakkelijker. Bij de meeste standaardmodules van een ESP32 worden deze chips gebruikt.

Het standaardschema is open source gezet door de fabrikant, wat een goede gelegenheid biedt om de CP2102-chip te verwerken met het Sparkfunschema. Het programmatienetwerk is hier aan verbonden. Figuur 21 [24]

### 2.2.4 ST7920

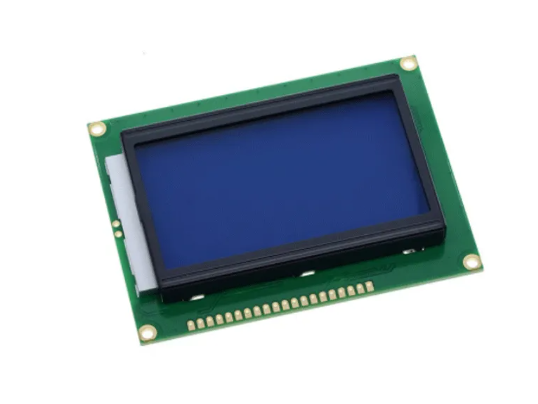
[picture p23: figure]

Figuur 22: ST7920 lcd [25]

De ESP32-S2 heeft meerdere SPI-poorten, de ST7920 lcd werkt via dit protocol. [25] Het is interessant om te weten welke pinnen van de chip daarvoor in gebruik worden gesteld zonder extra instellingen te moeten doen. Er is namelijk maar één poort die wordt verbonden en rechtstreeks kan worden geprogrammeerd zonder aanpassingen te moeten doen of zonder extra commando’s te schrijven naar de ESP. Figuur 22 Figuur 2326]

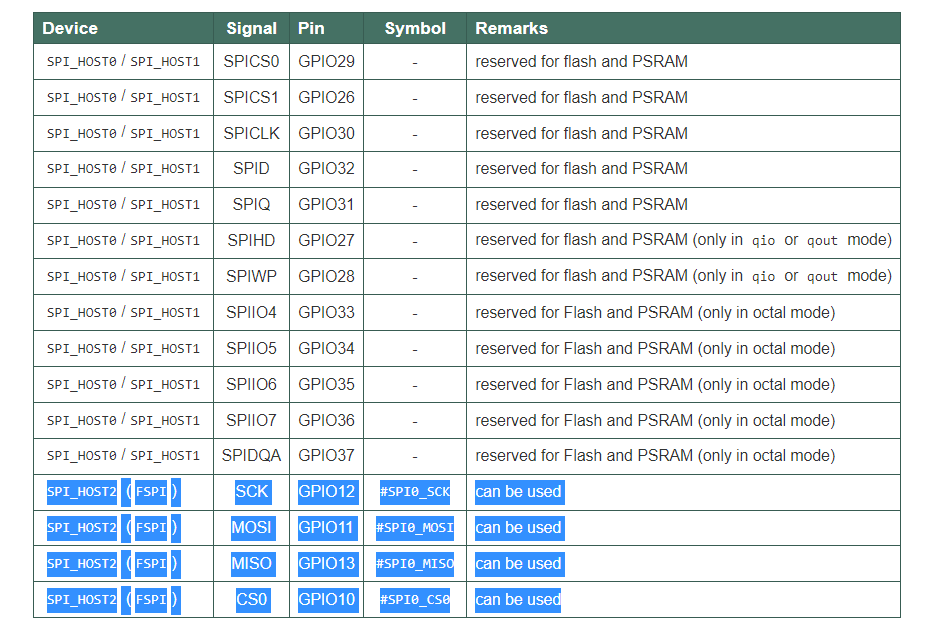
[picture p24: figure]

Figuur 23:SPI pinnen [26]

### 2.2.5 Rotary encoder


Figuur 24: Rotary encoder schema [27]

De rotary aansturen is vrij eenvoudig, enkele GPIO-pinnen zijn voldoende om alle data in te lezen. Om een rotary encoder aan te sturen zonder dat die op een pcb gemonteerd is, zoals op onderstaande foto, moeten nog enkele weerstanden worden toegevoegd. Figuur 24 Figuur 25 [27] [28]


Figuur 25: Rotary encoder op pcb [28]

## 2.3 BOM (Bill of Materials)

De BOM is een stukkenlijst die is opgesteld voor elk gebruikt component.

Een stukkenlijst is van groot belang om een idee te krijgen van het kostenplaatje van het project. Doordat de linkt elke keer vermeld staat bij het product, is het praktisch om alles makkelijk terug te vinden en daarom is de prijs per stuk en de algemene prijs weergegeven.
Een groot deel van de componenten is aangekocht bij AliExpress omdat dit goedkoper is.

Om de gebruikte BOM te bekijken, wordt verwezen naar Bijlage 2

## 2.4 Schema

Het schema is te vinden in Bijlage 3.

Om het schema te realiseren wordt gebruik gemaakt van het programma Eagle. Met de software van het bedrijf Autodesk is het mogelijk om een elektronisch schema te maken dat naar een boarddesign kan worden omgezet. Autodesk biedt de service Fusion 360 aan die het toestaat om een board design te converteren naar een 3D-ontwerp, wat het tekenen van een behuizing vereenvoudigd.

Om het elektronisch schema geordend te houden, wordt het blad opgedeeld door stippellijnen, per vak staat er een naam van het circuit. Een connectie kan worden gemaakt met een draad of met labels, alle labels met dezelfde naam zijn doorverbonden. Eveneens zijn alle gebruikte pinnen extern beschikbaar om metingen te doen of om apparatuur op aan te sluiten.

De bedoeling is dat de USB-C-connector dient om de microcontroller te programmeren. Dit is een standaard aan het worden zoals aangekaart bij hoofdstuk 1.2.1. Het is makkelijk in gebruik, aangezien het niet uitmaakt hoe de kabel in de poort wordt gestoken, het werkt altijd.

Om het circuit te programmeren, wordt gebruik gemaakt van 2 knoppen die dienen om een programma op de chip te plaatsen. De ene pin is een bootpin en de andere pin is een resetpin. Deze knoppen worden niet gebruikt, aangezien dit proces door twee transistoren kan worden geautomatiseerd. Als back-up zijn er wel nog twee knoppen aanwezig.

Enkele belangrijke componenten zijn elco‘s en keramische condensatoren. Lage capaciteiten tussen pico- en microfarad zorgen ervoor om ruis weg te filteren, de spanning te stabiliseren en DC-signalen te blokkeren.

Hoge capaciteiten (bereik van enkele farads) zorgen ervoor dat er bepaalde lading kan worden opgeslaan.

Er is ook een sense weerstand aanwezig in het project met een weerstand van 0,11 ohm. Er wordt gebruik gemaakt van twee weerstanden, één voor spoel A in de motor en één voor spoel B in de motor. Op die manier kan de stroom in de spoel worden gemeten. Figuur 26 [29]

Figuur 26: Spoelen in een stappenmotor [29]

## 2.5 Board design

De printplaat is te vinden in Bijlage 4.

Door het grote aantal componenten en de plaatsing van de pcb wordt er een 4-lagen pcb ontworpen. Een 4-lagen pcb is een printplaat met vier lagen koperen geleiders en wordt vaak gebruikt voor complexe elektronica. Bij het ontwerpproces zijn er verschillende belangrijke factoren om rekening mee te houden.

Allereerst is de lay-out van het pcb van groot belang. Het ontwerp moet zorgvuldig worden gepland om ervoor te zorgen dat alle onderdelen op de juiste manier kunnen worden geplaatst en verbonden. De plaatsing en routing van de koperbanen kan van groot belang zijn voor de prestaties van de pcb. In dit project wordt gebruik gemaakt van een lcd van 93 mm x 70 mm om op de pcb te plaatsen. Dit betekent dan de componenten met koelelementen zorgvuldig moesten worden gepositioneerd om te voorkomen dat ze in de weg staan van de lcd.


Een andere belangrijke factor is thermische beheersing. Op de printplaat staan enkele componenten die warmte genereren, dus moet ervoor worden gezorgd dat de warmteafvoer van deze componenten goed verloopt en dat ze geen problemen veroorzaken. Dit kan worden bereikt door het gebruik van koperbanen en thermische pads, die op hun beurt de warmteafvoer verbeteren en voorkomen dat de componenten oververhit raken.

Daarnaast is stroomvoorziening een cruciale factor bij het ontwerpen van een pcb. Tijdens het ontwerp werd er rekening mee gehouden dat de voedingsbanen op de pcb dik genoeg zijn, zodat deze banen niet doorbranden als er teveel stroom door loopt. Dit kan worden bereikt door het gebruik van brede koperbanen. Deze koperbanen werden berekend door gebruik te maken van een pcb-trace width calculator.

Er moeten een aantal gegevens zoals de hoeveelheid stroom die de koperbaan verdraagt en de dikte van de pcb worden ingeven. Na het invullen van de gegevens, is de vaststelling dat er een baandikte moet worden voorzien van 0,0385 mm.

Figuur 27 [30]

Figuur 27: Calculator voor baandikte [30]

# 3 Realisatie

## 3.1 Bestukking

## 3.2 Programmatie

## 3.3 Motoren

# 4 Testen

## 4.1 Connecties

## 4.2 Veiligheid

## 4.3 Functionaliteit

## 4.4 Programmatie

## 4.5 Mechanische onderdelen

Conclusie

Literatuurlijst

[1] | S. P. Dinkgreve, „wetenschapsschool,” Natuurkunde voor de Middelbare School, 2018. [Online]. Available: https://ap.lc/MHHQ6. [Geopend 2023 maart 29].
[2] | „Domoticx,” [Online]. Available: https://ap.lc/deZqp. [Geopend 17 Maart 2023].
[3] | „Tinytronics,” [Online]. Available: https://ap.lc/eTqNZ. [Geopend 17 maart 2023].
[4] | „Tinytronics,” [Online]. Available: https://ap.lc/3loJv. [Geopend 17 maart 2023].
[5] | „Conrad,” [Online]. Available: https://ap.lc/pZaYL. [Geopend 17 maart 2023].
[6] | „Arduino,” [Online]. Available: https://ap.lc/OHA2n. [Geopend 18 maart 2023].
[7] | „Tinytronics,” [Online]. Available: https://ap.lc/gQWu6. [Geopend 18 maart 2023].
[8] | „Digikey,” [Online]. Available: https://ap.lc/i7Pd2. [Geopend 20 maart 2023].
[9] | C. B.-S. 4. Chindi.ap, „Arrow,” 2018 november 19. [Online]. Available: https://ap.lc/Hhr6j. [Geopend 2023 maart 28].
[10] | „Mouser,” STMicroelectronics, 2021. [Online]. Available: https://ap.lc/08Oq4. [Geopend 20 maart 2023].
[11] | „Mchobby,” [Online]. Available: https://ap.lc/jClrO. [Geopend 17 maart 2023].
[12] | M. K. C. G. M. Dhruti Ranjan Gaan, „semanticscholar,” 2017. [Online]. Available: https://ap.lc/3FZnb. [Geopend 2023 maart 28].
[13] | „Alldatasheet,” [Online]. Available: https://ap.lc/CW7Hs. [Geopend 17 maart 2023].
[14] | „Robotic arms,” [Online]. Available: https://ap.lc/cL01R. [Geopend 21 maart 2023].
[15] | R. Vaughn, „Machinedesign,” Machinedesign, 2 december 2013. [Online]. Available: https://ap.lc/Xp3Y1. [Geopend 21 maart 2023].
[16] | „Go to shoping,” [Online]. Available: https://ap.lc/ZoN4D. [Geopend 21 maart 2023].
[17] | M. Claussen, „Elektormagazine,” Elektormagazine, 12 juli 2022. [Online]. Available: https://ap.lc/lHw1e. [Geopend 21 maart 2023].
[18] | „Kuka,” Kuka, [Online]. Available: https://ap.lc/gyjYQ. [Geopend 21 maart 2023].
[19] | T. Nardi, „Hackaday,” Hackaday, 19 oktober 2020. [Online]. Available: https://ap.lc/UFSXb. [Geopend 21 maat 2023].
[20] | G. Klop, „Pure.tue,” Tue, 1992 januari 01. [Online]. Available: https://ap.lc/0subo. [Geopend 2023 maart 29].
[21] | Sparkfun, „Sparkfun,” Sparkfun, [Online]. Available: https://ap.lc/GlkWh. [Geopend 19 mei 2023].
[22] | Espressif, „Espressif,” Espressif systems, 2023. [Online]. Available: https://ap.lc/W5mUX. [Geopend 19 mei 2023].
[23] | TRINAMIC, „Digikey,” Digikey, 12 2017. [Online]. Available: https://www.digikey.be/reference-designs/en/motor-control/motor-control/2276. [Geopend 18 mei 2023].
[24] | Espressif, „Espressif,” Espressif systems, 06 December 2012. [Online]. Available: https://ap.lc/yFm0c. [Geopend 20 mei 2023].
[25] | Blaisebaette, „Instructables,” [Online]. Available: https://ap.lc/KWCGc. [Geopend 20 mei 2023].
[26] | G. Schorcht, „Riot,” [Online]. Available: https://ap.lc/q2g6g. [Geopend 20 mei 2023].
[27] | Robotics, „robotics,” [Online]. Available: https://ap.lc/yF6s1. [Geopend 21 mei 2023].
[28] | Pishop, „Pishop,” [Online]. Available: https://ap.lc/FYUwR. [Geopend 22 mei 2023].
[29] | TME, „TME,” TME, 08 augustus 2020. [Online]. Available: https://ap.lc/VQVPt. [Geopend 22 mei 2023].
[30] | „circuitcalculator,” 31 januari 2006. [Online]. Available: https://ap.lc/aBSjM. [Geopend 23 mei 2023].
[31] | Y. YAKIMOVA, „Europees parlement,” Europees parlement, 07 juni 2022. [Online]. Available: https://ap.lc/BxmRq. [Geopend 20 maart 2023].
[32] | „almotion,” almotion, [Online]. Available: https://ap.lc/amwzP. [Geopend 2023 maart 28].
[33] | „zvstechniek,” zvstechniek, [Online]. Available: https://ap.lc/gdEbe. [Geopend 2023 maart 28].

Bijlagenoverzicht

## Bijlage 1: Kopieën datasheets

Bijlage 1: nog in te vullen

## Bijlage 2: BOM

Tabel 5: BOM

Product | Type | Link | Stuks | Prijs | Prijs/stuk | Gebruikte stuks | Totaalprijs per gebruikte stuks
Voedingsstekker | SMD | https://nl.aliexpress.com/item/4000677508616.html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 | 10 | € 1,44 | € 0,144 | 1 | € 0,144
CP2102 | SMD | https://nl.aliexpress.com/item/33000297490.html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 | 3 | € 4,47 | € 1,49 | 1 | € 1,49
USB-C-poort | SMD | https://nl.aliexpress.com/item/1005004804811591.html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 | 10 | € 0,54 | € 0,054 | 1 | € 0,054
Jumper | THT | https://nl.aliexpress.com/item/1005004985941167.html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 | 100 | € 0,74 | € 0,0074 | 2 | € 0,0148
Rotary encoder | THT | https://nl.aliexpress.com/item/10000056483250.html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 | 5 | € 0,71 | € 0,142 | 1 | € 0,142
Pottrimmer voor TMC2208 | SMD | https://nl.aliexpress.com/item/1005002763769561.html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 | 20 | € 1,81 | € 0,0905 | 3 | € 0,2715
Meetweerstand voor TMC2208 | SMD | https://nl.aliexpress.com/item/1005003411558149.html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 | 100 | € 0,54 | € 0,0054 | 3 | € 0,0162
Leds | SMD | https://nl.aliexpress.com/item/1005003327360045.html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 | 100 | € 2,28 | € 0,0228 | 4 | € 0,08912
5 V-LDO | SMD | https://nl.aliexpress.com/item/1005004908874511.html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 | 50 | € 1,47 | € 0,0294 | 1 | € 0,0294
3.3 V -LDO | SMD | https://nl.aliexpress.com/item/1005004908874511.html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 | 50 | € 1,47 | € 0,0294 | 2 | € 0,0588
TMC2208-chip | SMD | https://nl.aliexpress.com/item/1005002873631753.html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 | 10 | € 10,24 | € 1,024 | 3 | € 3,072
ESP32-S2-wroom | SMD | https://nl.aliexpress.com/item/1005002221813688.html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 | 3 | € 7,23 | € 2,41 | 1 | € 2,41
Knop | SMD | https://nl.aliexpress.com/item/4000700060759.html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 | 10 | € 1,37 | € 0,137 | 2 | € 0,274
Condensatoren | SMD | https://nl.aliexpress.com/item/4001345918046.html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 | 720 | € 6,89 | € 0,009 | 37 | € 0,333
Weerstanden | SMD | https://nl.aliexpress.com/item/1005001461098423.html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 | 2000 | € 5,02 | € 0,025 | 33 | € 0,825
lcd ST7920 | THT | https://nl.aliexpress.com/item/1005003916378097.html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 | 1 | € 4,91 | € 4,91 | 1 | € 4,91
Servo MG995 | THT | https://www.bol.com/be/nl/p/azdelivery-3-x-mg995-micro-digital-servo-motor-voor-rc-robots-helikoptervliegtuigen-compatibel-met-arduino-inclusief-e-book/9300000119725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 | 3 | € 19,99 | € 6,66 | 3 | € 19,99
BC547 | THT | https://nl.aliexpress.com/item/1005003458995298.html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 | 100 | € 0,65 | € 0,0065 | 2 | € 0,013
Elco | THT | https://nl.aliexpress.com/item/32803428396.html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 | 200 | € 3,81 | € 0,019 | 2 | € 0,038
Tactile shakelaar | THT | https://nl.aliexpress.com/item/1005003938244847.html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 | 20 | € 1,52 | € 0,076 | 1 | € 0,076
Stappenmotoren 17HS4401 | THT | https://nl.aliexpress.com/item/32665922113.html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 | 3 | € 27 | € 9 | 3 | € 27
Pcb | BOARD | https://jlcpcb.com/ | 5 | € 28,04 | € 5,608 | 1 | € 5,608
Totaal | € 66,85882

Bijlage 2: BOM

## Bijlage 3: Schema


Bijlage 3: Schema's

Figuur 28: Schema deel1


Figuur 29: Schema deel2 Bijlage 3


Figuur 30: Schema deel3 Bijlage 3


Figuur 31: Schema deel4 Bijlage 3


Figuur 32: Schema deel5 Bijlage 3

## Bijlage 4: Pcb


Bijlage 4: Pcb

Figuur 33: Pcb

## Bijlage 5: Logboek rapporteren

Lesweek 7: 13/02 – 19/02

Naam student | Paginanummers in rapport | Taak (bijv. schrijven klad, verbeteren, volledig herschrijven, nakijken, ...)
Lennert De Geeter | Vragenronde op school | Extra informatie vragen om een goed verslag op te stellen.
Roy De Volder | Vragenronde op school | Extra informatie vragen om een goed verslag op te stellen.
Jorik Van Dorpe | Vragenronde op school | Extra informatie vragen om een goed verslag op te stellen.
Lukas Verschraegen | Vragenronde op school | Extra informatie vragen om een goed verslag op te stellen.

Lesweek 8: 20/02 – 26/02

Naam student | Paginanummers in rapport | Taak (bijv. schrijven klad, verbeteren, volledig herschrijven, nakijken, ...)
Lennert De Geeter | Geen paginanummers (enkel brainstormen) | Brainstormen op papier/ digitaal op een tekentablet.
Roy De Volder | Geen paginanummers (enkel brainstormen) | Brainstormen op papier/ digitaal op een tekentablet.
Jorik Van Dorpe | Geen paginanummers (enkel brainstormen) | Brainstormen op papier/ digitaal op een tekentablet.
Lukas Verschraegen | Geen paginanummers (enkel brainstormen) | Brainstormen op papier/ digitaal op een tekentablet.

Lesweek 9: 27/02 - 5/03

Naam student | Paginanummers in rapport | Taak (bijv. schrijven klad, verbeteren, volledig herschrijven, nakijken, ...)
Lennert De Geeter | Pagina 7 | Inleiding
Roy De Volder | Pagina 1,3 | Hoofdblad opstellen
Jorik Van Dorpe | Pagina 1-11 | Controle
Lukas Verschraegen | Pagina 1-11 | Opstellen van het document volgens de regels uit het boek.

Lesweek 10: 5/03 - 12/03

Naam student | Paginanummers in rapport | Taak (bijv. schrijven klad, verbeteren, volledig herschrijven, nakijken, ...)
Lennert De Geeter | Pagina 23-25 | Het schrijven van een kladversie.
Roy De Volder | Pagina 26-28 | Het schrijven van een kladversie.
Jorik Van Dorpe | Pagina 22 | Het schrijven van een kladversie.
Lukas Verschraegen | Pagina 13-21 | Het schrijven van een kladversie.

Lesweek 11: 13/03 - 19/03

Naam student | Paginanummers in rapport | Taak (bijv. schrijven klad, verbeteren, volledig herschrijven, nakijken, ...)
Lennert De Geeter | Pagina 23-25 | Het herschrijven naar een correcte versie.
Roy De Volder | Pagina 26-28 | Het herschrijven naar een correcte versie.
Jorik Van Dorpe | Pagina 22 | Het herschrijven naar een correcte versie.
Lukas Verschraegen | Pagina 13-21 | Het herschrijven naar een correcte versie.

Lesweek 12: 20/03 - 26/03

Naam student | Paginanummers in rapport | Taak (bijv. schrijven klad, verbeteren, volledig herschrijven, nakijken, ...)
Lennert De Geeter | Pagina 13-19 | Nakijken tekst.
Roy De Volder | Pagina 7-11 / 30 | Controle van de lay-out.
Jorik Van Dorpe | Pagina 20-28 | Nakijken tekst.
Lukas Verschraegen | Pagina 7-11 / 30 | Opstellen van de lijsten volgens de regels uit het boek en verbeteren tekst.

Lesweek 13: 27/03 – 2/04

Naam student | Paginanummers in rapport | Taak (bijv. schrijven klad, verbeteren, volledig herschrijven, nakijken, ...)
Lennert De Geeter | Pagina 13-28 | Verbeteren van fouten
Roy De Volder | Pagina 13-28 | Verbeteren van fouten
Jorik Van Dorpe | Pagina 13-28 | Verbeteren van fouten
Lukas Verschraegen | Pagina 13-28 | Verbeteren van fouten

Lesweek 14: 3/04 – 9/04

Naam student | Paginanummers in rapport | Taak (bijv. schrijven klad, verbeteren, volledig herschrijven, nakijken, ...)
Lennert De Geeter | Pagina 7-11, 40-42 | Lijsten bijwerken
Roy De Volder | Pagina 38 | Schrijven van kladversie
Jorik Van Dorpe | Pagina 7-11, 40-42 | Lijsten bijwerken
Lukas Verschraegen | Pagina 29-37 | Schrijven van kladversie

Lesweek 15: 10/04 – 16/04

Naam student | Paginanummers in rapport | Taak (bijv. schrijven klad, verbeteren, volledig herschrijven, nakijken, ...)
Lennert De Geeter | Pagina 29-38 | Nakijken
Roy De Volder | Pagina 38 | Verder schrijven aan kladversie
Jorik Van Dorpe | Pagina 29-38 | Nakijken
Lukas Verschraegen | Pagina 29-37 | Verder schrijven aan kladversie

Lesweek 16: 17/04 – 23/04

Naam student | Paginanummers in rapport | Taak (bijv. schrijven klad, verbeteren, volledig herschrijven, nakijken, ...)
Lennert De Geeter | Pagina 29-38 | Nakijken op fouten
Roy De Volder | Pagina 38 | Herschrijven naar correcte versie
Jorik Van Dorpe | Pagina 29-38 | Nakijken op fouten
Lukas Verschraegen | Pagina 29-37 | Herschrijven naar correcte versie

Lesweek 17: 24/04 – 30/04

Naam student | Paginanummers in rapport | Taak (bijv. schrijven klad, verbeteren, volledig herschrijven, nakijken, ...)
Lennert De Geeter | Pagina 29-37 | Nakijken tekst
Roy De Volder | Pagina 29-38 | Nakijken op tekst en inhoud
Jorik Van Dorpe | Pagina 29-37 | Nakijken op Inhoud
Lukas Verschraegen | Pagina 29-38 | Controleren op fouten en lay-out in orde stellen

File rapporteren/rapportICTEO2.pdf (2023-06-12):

Professionele bachelor Elektronica-ICT

Academiejaar: 2022 / 2023

# Het maken en sturen van een robotarm

Lectoren: | Sabine Martens Mario Wyns
Verslaggevers: | Lennert De Geeter Roy De Volder Jorik Van Dorpe Lukas Verschraegen
Klas: | 3ELO

Professionele bachelor Elektronica-ICT

Academiejaar: 2022 / 2023

# Het maken en sturen van een robotarm

Lectoren: | Sabine Martens Mario Wyns
Verslaggevers: | Lennert De Geeter Roy De Volder Jorik Van Dorpe Lukas Verschraegen
Klas: | 3ELO

## Abstract

The creation and control of a robotic arm.

L. De Geeter, R. De Volder, J. Van Dorpe, L. Verschraegen
This work is an exhaustive exploration into the design, the creation and testing of a fully custom-built robotic arm with the objective of advancing our understanding and improving techniques in the field of robotics. The study commences with in-depth research into various types of motors, including stepper motors, servo motors, DC motors and brushless DC motors,

The research delves into the mechanical aspects of the project, examining the Cartesian robotic arm, the articulated robotic arm, and the SCARA robotic arm. The safety considerations are also analysed in detail. The design process is then illustrated, beginning with the creation of a block diagram, identification and detailed discussion of key components like the ESP32-S2, TMC2208, CP2102, ST7920, and rotary encoder. A comprehensive bill of materials (BOM) is provided, followed by a schematic representation and a pcb-design of the system that controls the robotic arm.

The realization section documents the assembly of the robotic arm, discussing the programming of the system and the integration of the motors. The report follows up with an extensive series of tests, including connectivity, safety measures, functionality, programming and mechanical parts.

The document concludes with an objective synthesis of the findings and their wider implications. Additional supporting materials, including copies of datasheets, the BOM, schematic diagrams and pcb-design, are included in the appendices. This investigation offers a detailed overview of the development and operation of a custom robotic arm system, providing a useful resource for future developments in the field of robotics.

Keywords: robotic arm system, pcb-design, 3D-design, schematic representation, assembly, functional testing, robotics, communication protocols

## Inhoudsopgave

Figurenlijst | 7
Tabellenlijst | 9
Codefragmentenlijst | 10
Afkortingenlijst | 11
Begrippenlijst | 13
Inleiding | 14
1 | Onderzoek | 15
1.1 | Motoren | 15
1.1.1 | Stappenmotor | 16
1.1.2 | Servomotor | 16
1.1.3 | DC-motoren | 16
1.1.4 | Brushless DC-motoren | 16
1.2 | Sensoren | 19
1.2.1 | Voeding | 21
1.2.2 | Communicatie | 23
1.2.3 | Programmatiecircuit | 23
1.2.4 | Sensor voor het aansturen van de stappenmotor | 24
1.3 | Mechanica | 25
1.3.1 | Cartesische robotarm | 25
1.3.2 | Articulated robotarm | 26
1.3.3 | SCARA-robotarm | 27
1.4 | Veiligheid | 28
1.5 | Opzetstuk | 29
2 | Ontwerp | 31
2.1 | Blokschema | 31
2.2 | Componenten | 33
2.2.1 | TMC2208 | 34
2.2.2 | CP2102 | 35
2.2.3 | ST7920 | 36
2.2.4 | Rotary encoder | 37
2.3 | Mechanisch ontwerp | 38
2.4 | BOM (Bill of Materials) | 40
2.5 | Schema | 41
2.6 | Board design | 42
3 | Realisatie | 43
3.1 | Bestukking | 43
3.2 | Programmatie | 45
3.3 | Motoren | 49
4 | Testen | 50
4.1 | Connecties | 50
4.2 | Werking | 51
4.3 | Veiligheid | 52

Onderzoek | 6
4.4 | Functionaliteit | 53
4.5 | Programmatie | 54
4.6 | Mechanische onderdelen | 55
Conclusie | 56
Literatuurlijst | 57
Bijlagenoverzicht | 60
Bijlage 1: Kopieën datasheets | 60
Bijlage 2: BOM | 63
Bijlage 3: Schema | 67
Bijlage 4: Pcb | 72
Bijlage 5: Logboek rapporteren | 73

## Figurenlijst

Figuur 1: Arduino mkr wifi 1010 [6] | | 19 (https://hubkaho-my.sharepoint.com/personal/roy_devolder_student_odisee_be/Documents/PWR/rapporteren/Het%20maken%20en%20sturen%20van%20een%20robotarm%20versie1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)
Figuur 2: ESP32 [7] | | 19 (https://hubkaho-my.sharepoint.com/personal/roy_devolder_student_odisee_be/Documents/PWR/rapporteren/Het%20maken%20en%20sturen%20van%20een%20robotarm%20versie1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)
Figuur 3: ESP32-WROOM-32D chip zonder pcb [8] | 21
Figuur 4: USB-C-pinout [9] | | 21
Figuur 5: Typische applicatie LDO [10] | | 22
Figuur 6: Full-step vs. micro-step [12] | | 24
Figuur 7: Verschillende types robotarmen [14] | 25
Figuur 8: Cartesische robotarm en de aluminium profielen [16] [15] | 25 (https://hubkaho-my.sharepoint.com/personal/roy_devolder_student_odisee_be/Documents/PWR/rapporteren/Het%20maken%20en%20sturen%20van%20een%20robotarm%20versie1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)
Figuur 9: LumenPnP cartesische robotarm [17] | 26
Figuur 10: Lasrobot [18] Figuur 11: Assemblagerobot [18] | 26
Figuur 12: Scara-robotarm [15] | | 27 (https://hubkaho-my.sharepoint.com/personal/roy_devolder_student_odisee_be/Documents/PWR/rapporteren/Het%20maken%20en%20sturen%20van%20een%20robotarm%20versie1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)
Figuur 13: Uitgewerkt versie PyBot [19] | Figuur 14: 3D-Assenstelsel [19] | 27
Figuur 15: Parallelle grijper [36] | | 29 (https://hubkaho-my.sharepoint.com/personal/roy_devolder_student_odisee_be/Documents/PWR/rapporteren/Het%20maken%20en%20sturen%20van%20een%20robotarm%20versie1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)
Figuur 16: Pneumatische hoek-grijper [37] | | 29 (https://hubkaho-my.sharepoint.com/personal/roy_devolder_student_odisee_be/Documents/PWR/rapporteren/Het%20maken%20en%20sturen%20van%20een%20robotarm%20versie1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)
Figuur 17: Blokschema | | 31

Figuur 18: SparkFun Thing Plus - ESP32-S2 WROOM [21] Figuur 19: ESP32-S2 chip [22] 33

Figuur 20: Digikey TMC2208 board [23] | | 34
Figuur 21: CP2102 schema [24] | | 35
Figuur 22: ST7920 lcd [25] | | 36
Figuur 23: SPI pinnen [26] | | 36
Figuur 24: Rotary encoder schema [27] | | 37
Figuur 25: Rotary encoder op pcb [28] | | 37
Figuur 26: Uitwerking met geprinte vertanding | 38 (https://hubkaho-my.sharepoint.com/personal/roy_devolder_student_odisee_be/Documents/PWR/rapporteren/Het%20maken%20en%20sturen%20van%20een%20robotarm%20versie1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)
Figuur 27: Uitwerking met motoren | | 38
Figuur 28: Connectie tussen de assen met buizen | 39
Figuur 29: Grijper | | 39
Figuur 30: Spoelen in een stappenmotor [29] | 41
Figuur 31: Calculator voor baandikte [31] | | 42
Figuur 32: Stencil voor de pcb | | 43 (https://hubkaho-my.sharepoint.com/personal/roy_devolder_student_odisee_be/Documents/PWR/rapporteren/Het%20maken%20en%20sturen%20van%20een%20robotarm%20versie1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)
Figuur 33: Pcb met soldeerpasta | | 44

Onderzoek | 8
Figuur 34: Werkend resultaat van de gesoldeerde pcb | 44
Figuur 35: Volledige vierde as met servomontage en doorsnede met analyse | 49
Figuur 36: TMC2208 risico | 51 (https://hubkaho-my.sharepoint.com/personal/roy_devolder_student_odisee_be/Documents/PWR/rapporteren/Het%20maken%20en%20sturen%20van%20een%20robotarm%20versie1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)
Figuur 37: Back-upplan | 51
Figuur 38: Veiligheidsicoon hitte | 52
Figuur 39: Eindresultaat robotarm | 55 (https://hubkaho-my.sharepoint.com/personal/roy_devolder_student_odisee_be/Documents/PWR/rapporteren/Het%20maken%20en%20sturen%20van%20een%20robotarm%20versie1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)
Figuur 40: Opsplitsen van een ontwerp | 55
Figuur 41: Schema deel1 | 67
Figuur 42: Schema deel2 Bijlage 5 | 68
Figuur 43: Schema deel3 Bijlage 5 | 69
Figuur 44: Schema deel4 Bijlage 5 | 70
Figuur 45: Schema deel5 Bijlage 5 | 71
Figuur 46: Pcb | 72

## Tabellenlijst

Tabel 1: Afkortingenlijst | 11
Tabel 2: Begrippenlijst | 13
Tabel 3: Vergelijking van motoren [2] [3] [4] [5] | 17
Tabel 4: Microcontrollers vergelijken [6] [7] | 20
Tabel 5: BOM | 63

## Codefragmentenlijst

Codefragment 1: Toevoegen bibliotheken [32] [33] | 45
Codefragment 2: Initialisatie stappenmotoren en servomotoren [32] [33] | 45
Codefragment 3: Definiëren knoppen en variabelen aanmaken | 45

Codefragment 4: Definiëren led en potentiometers en variabelen voor de potentiometers 46

Codefragment 5: Definiëren variabelen voor posities | 46
Codefragment 6: Definiëren variabelen voor posities [32] [33] | 47
Codefragment 7: Definiëren variabelen voor posities [32] [33] | 47
Codefragment 8: Indrukken van de save knop | 48
Codefragment 9: Indrukken van de save knop | 48
Codefragment 10: Indrukken van de save knop [32] [33] | 48
Codefragment 11: Indrukken van de stop knop | 49
Codefragment 12: Indrukken van de save knop | 54

## Afkortingenlijst

Tabel 1: Afkortingenlijst

Afkorting | Betekenis
BOM | Bill of Materials
IC | Integrated circuit
DC | Direct current
PWM | Pulse-width modulation
MCU | Microcontroller unit
ESC | Electronic speed control
NEMA | National Electric Manufacturers' Association
pcb | Printed circuit board
IoT | Internet of Things
SoC | System-on-chip
SPI | Serial Peripheral Interface
I2C | Inter-Integrated Circuit
UART | Universal asynchronous receiver-transmitter
BLE | Bluetooth Low Energy
USB | Universal Serial Bus
LDO | Low-drop-out
TTL | Transistor-Transistor Logica
RMS | Root Mean Square

Onderzoek | 12
DIR | Direction
OTP | One-time programmable
SRAM | Static random-access memory
lcd | liquid crystal display
TMC | Trinamic
GPIO | General Purpose Input/ Output
elco | elektrolytische condensator

## Begrippenlijst

Tabel 2: Begrippenlijst

Begrip | Verklaring
Brushless | Geen gebruik maken van fysieke contacten naar de commutator van de motor.
Flash | Flash is de verzamelnaam voor opslagsystemen waar data wordt opgeslagen op chips die hun informatie behouden nadat de voedingsspanning is weggehaald. Het is een vorm van niet-vluchtig geheugen dat in 1984 voor het eerst op de markt kwam.
SRAM | Static random-access memory is een geheugen waarvan de inhoud niet periodiek hoeft geüpdatet worden. De opgeslagen data in een SRAM kunnen te allen tijde en in elke volgorde worden uitgelezen. Ze wijzigen enkel bij overschrijven of als de IC spanningsloos wordt. Het is dus een vluchtig geheugen.
Pinout | Pinout is een verwijzing naar de pinnen of contacten die een elektrisch apparaat of connector verbinden. Het beschrijft de functies van uitgezonden signalen en de circuit input/output (I/O) vereisten.
Royaltyvrij | Royaltyvrij is een term die wordt gebruikt om bepaalde soorten intellectuele eigendom te beschrijven zonder royalty's te betalen. Eigenaars van intellectuele eigendom moeten dit label specifiek op hun inhoud toepassen, zodat iedereen het op dezelfde manier kan gebruiken.
Beheersmaatregelen | Maatregelen die worden genomen om de risico's waaraan ondernemingen blootstaan te beheersen.
Consciëntie | Nauwkeurigheid.
SCARA | Selective Compliance Articulated Robot Arm
Interferentie | Interferentie is de samen- of tegenwerking van verscheidene golven op dezelfde tijd en plaats.
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

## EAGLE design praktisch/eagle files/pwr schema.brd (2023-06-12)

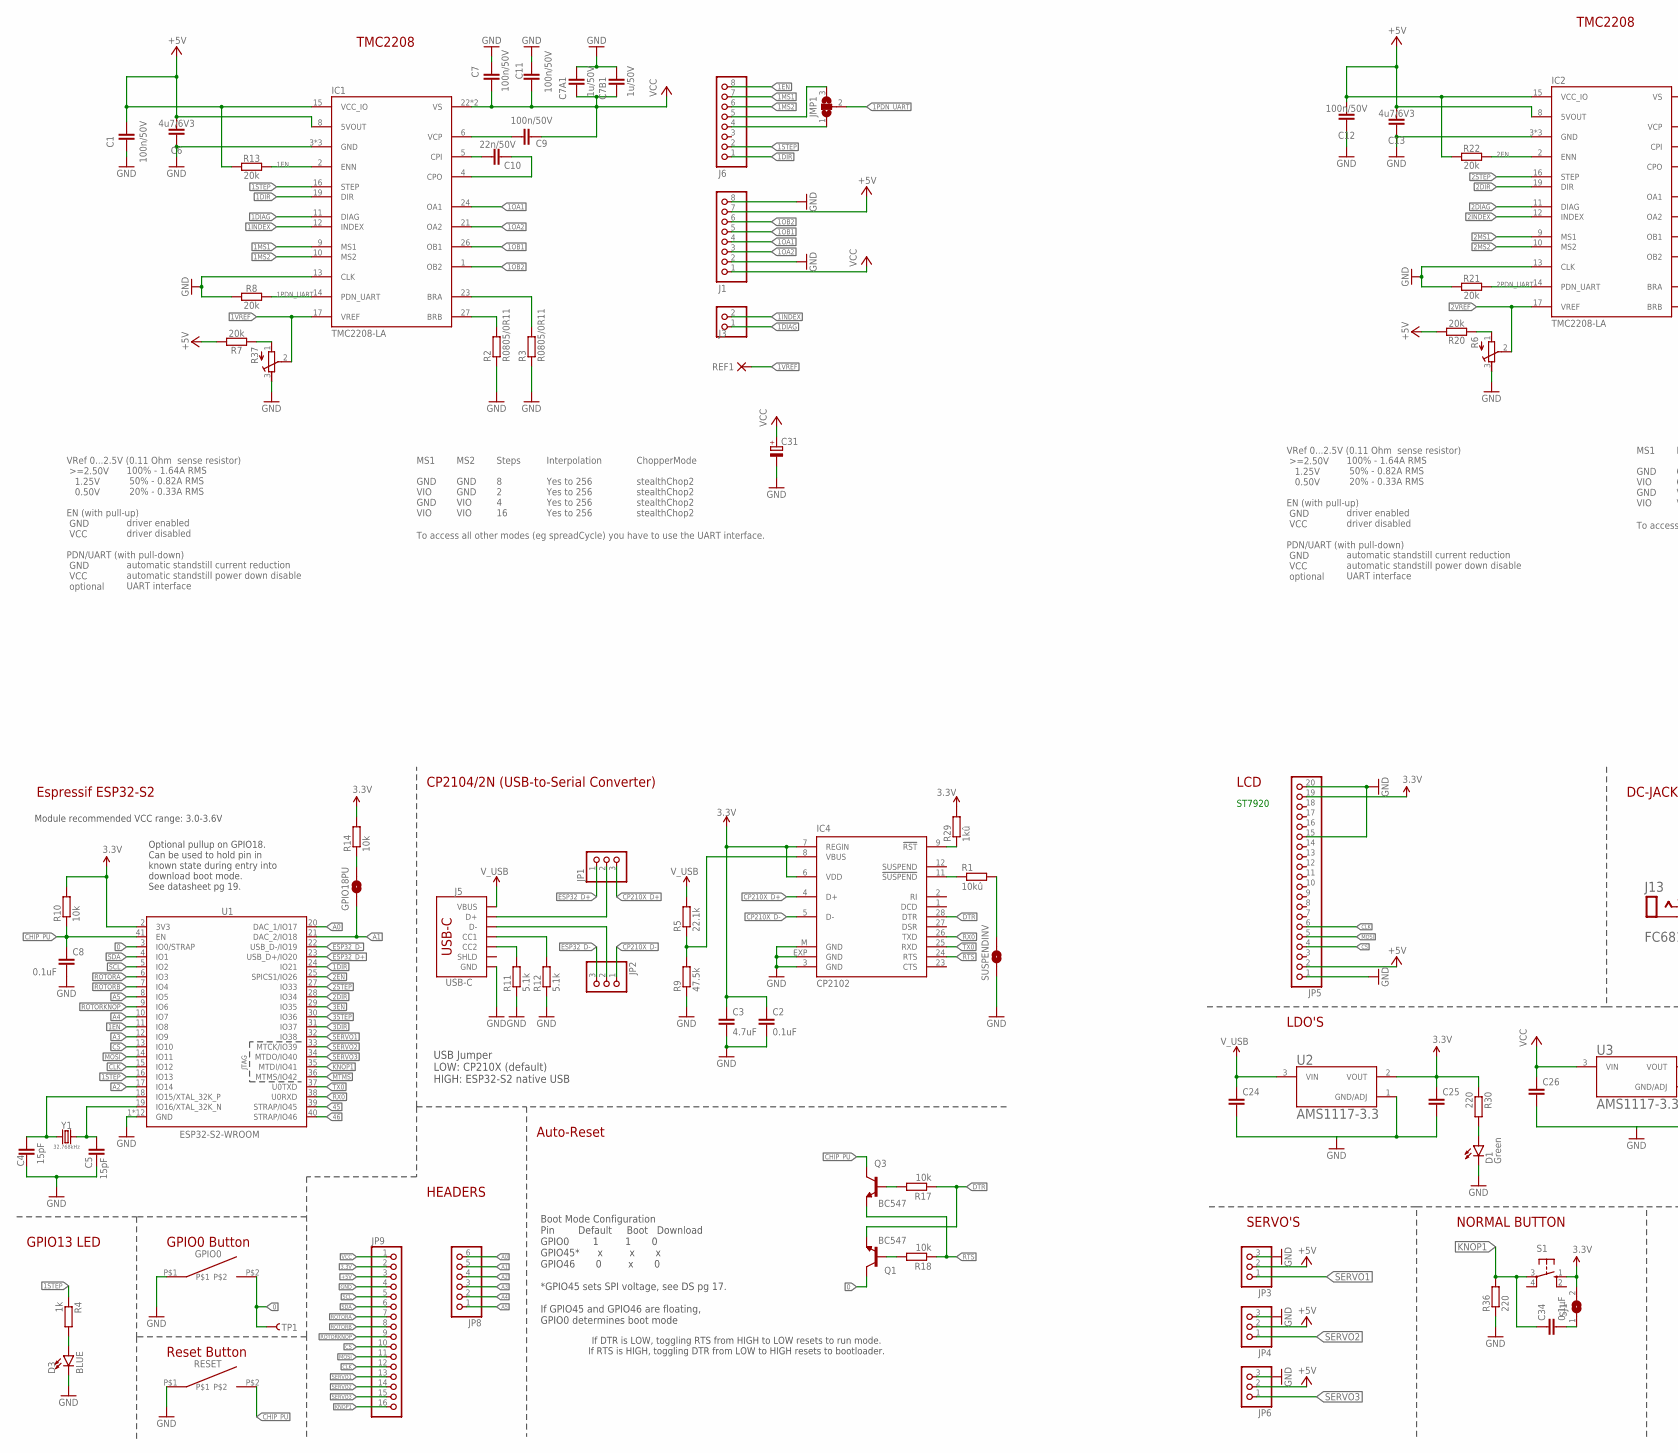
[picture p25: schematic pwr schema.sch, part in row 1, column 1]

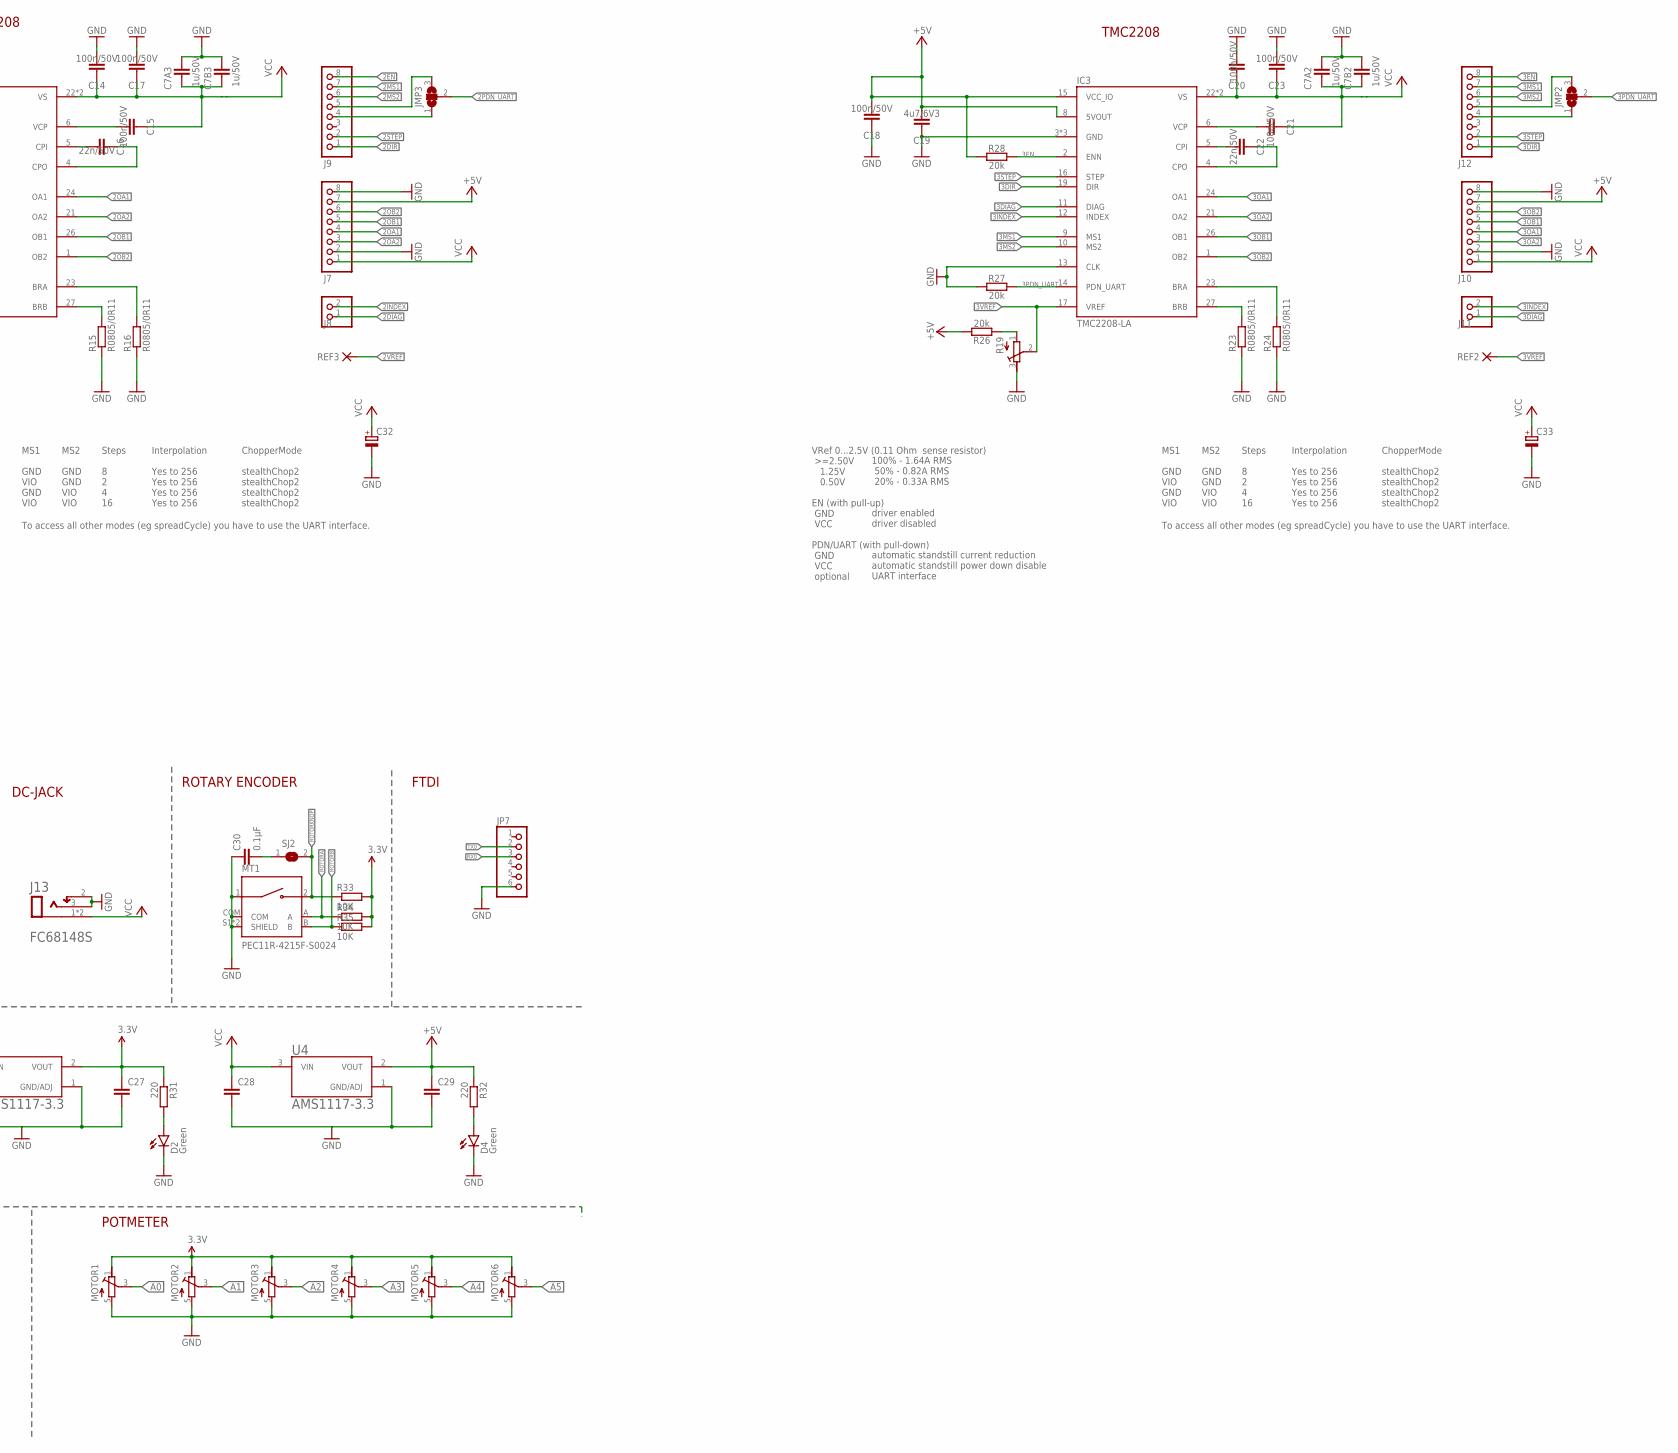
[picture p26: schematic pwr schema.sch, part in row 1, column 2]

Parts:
C1, C7, C9, C11, C12, C14, C15, C17, C18, C20, C21, C23: 100n/50V; C1206
C2, C8: 0.1uF; C1206
C3: 4.7uF; C1206
C4, C5: 15pF; C1206
C6, C13, C19: 4u7/6V3; C1206
C7A1, C7A2, C7A3, C7B1, C7B2, C7B3: 1u/50V; C1206
C10, C16, C22: 22n/50V; C1206
C24, C25, C26, C27, C28, C29: C-EUC1206; C1206
C30, C34: 0.1µF; C1206
C31, C32, C33: CPOL-EUE2.5-6; E2,5-6
D1, D2, D4: Green; CHIP-LED0603
D3: BLUE; LED-0603
GPIO0: SWITCHSMD3X6MM
GPIO18PU: JUMPER-SMT_2_NO_SILK; SMT-JUMPER_2_NO_SILK
IC1, IC2, IC3: TMC2208-LA; QFN28-PAD
IC4: CP2102; MLP28
J1, J6, J7, J9, J10, J12: PINHD-1X8; 1X08
J3, J8, J11: PINHD-1X2; 1X02
J5: USB-C; USB-C-16P-4LAYER-ISOLATED
J13: CLIFF_FC68148SCLIFF_FC68148S_0_0; CLIFF_FC68148S_0
JMP1, JMP2, JMP3: JUMPER3-0402-NC; JUMPER3-0402_NC
JP1, JP2, JP3, JP4, JP6: PINHD-1X3; 1X03
JP5: PINHD-1X20; 1X20
JP7, JP8: PINHD-1X6; 1X06
JP9: PINHD-1X16; 1X16
MOTOR1, MOTOR2, MOTOR3, MOTOR4, MOTOR5, MOTOR6: POTMETER
MT1: PEC11R-4215F-S0024; XDCR_PEC11R-4215F-S0024
Q1, Q3: BC547; TO92
R1: 10kû; R1206
R2, R3, R15, R16, R23, R24: R0805/0R11; R1206
R4: 1k; R1206
R5: 22.1k; R1206
R6, R19, R37: R-TRIMM3103; RTRIM3103
R7, R8, R13, R20, R21, R22, R26, R27, R28: 20k; R1206
R9: 47.5k; R1206
R10, R14, R17, R18: 10k; R1206
R11, R12: 5.1k; R1206
R29: 1kû; R1206
R30, R31, R32, R36: 220; R1206
R33, R34, R35: 10K; R1206
REF1, REF2, REF3: PAD-0.6-1.1
RESET: SWITCHSMD3X6MM
S1: 10-XX; B3F-10XX
SJ1, SJ2: SJ
SUSPENDINV: JUMPER-SMT_2_NO_SILK; SMT-JUMPER_2_NO_SILK
TP1: TEST-POINTTP_15TH_THRU; TP_15TH
U1: ESP32-S2-WROOM
U2, U3, U4: AMS1117-3.3; SOT229P700X180-4N
Y1: 32.768kHz; CRYSTAL-SMD-3.2X1.5MM

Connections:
0: GPIO0.P$2, Q1.3 (C), TP1.P$1, U1.3 (IO0/STRAP)
1BRA: IC1.23 (BRA), R3.2
1BRB: IC1.27 (BRB), R2.2
1CPI: C10.2, IC1.5 (CPI)
1CPO: C10.1, IC1.4 (CPO)
1DIAG: IC1.11 (DIAG), J3.1
1DIR: IC1.19 (DIR), J6.1, U1.24 (IO21)
1EN: IC1.2 (ENN), J6.8, R13.2, U1.11 (IO8)
1INDEX: IC1.12 (INDEX), J3.2
1MS1: IC1.9 (MS1), J6.7
1MS2: IC1.10 (MS2), J6.6
1OA1: IC1.24 (OA1), J1.4
1OA2: IC1.21 (OA2), J1.3
1OB1: IC1.26 (OB1), J1.5
1OB2: IC1.1 (OB2), J1.6
1PDN_UART: IC1.14 (PDN_UART), JMP1.2, R8.2
1STEP: IC1.16 (STEP), J6.2, R4.1, U1.16 (IO13)
1VCP: C9.2, IC1.6 (VCP)
1VREF: IC1.17 (VREF), R37.2 (S), REF1.1
1VREF1: R7.1, R37.1 (A)
2BRA: IC2.23 (BRA), R16.2
2BRB: IC2.27 (BRB), R15.2
2CPI: C16.2, IC2.5 (CPI)
2CPO: C16.1, IC2.4 (CPO)
2DIAG: IC2.11 (DIAG), J8.1
2DIR: IC2.19 (DIR), J9.1, U1.28 (IO34)
2EN: IC2.2 (ENN), J9.8, R22.2, U1.25 (SPICS1/IO26)
2INDEX: IC2.12 (INDEX), J8.2
2MS1: IC2.9 (MS1), J9.7
2MS2: IC2.10 (MS2), J9.6
2OA1: IC2.24 (OA1), J7.4
2OA2: IC2.21 (OA2), J7.3
2OB1: IC2.26 (OB1), J7.5
2OB2: IC2.1 (OB2), J7.6
2PDN_UART: IC2.14 (PDN_UART), JMP3.2, R21.2
2STEP: IC2.16 (STEP), J9.2, U1.27 (IO33)
2VCP: C15.2, IC2.6 (VCP)
2VREF: IC2.17 (VREF), R6.2 (S), REF3.1
2VREF1: R6.1 (A), R20.1
3.3V: C2.1, C3.1, C25.1, C27.1, IC4.6 (VDD), IC4.7 (REGIN), JP5.19, JP9.2, MOTOR1.1 (E), MOTOR2.1 (E), MOTOR3.1 (E), MOTOR4.1 (E), MOTOR5.1 (E), MOTOR6.1 (E), R10.2, R14.2, R29.2, R30.1, R31.1, R33.2, R34.2, R35.2, S1.1 (S), SJ1.2, U1.2 (3V3), U2.2 (VOUT), U3.2 (VOUT)
3BRA: IC3.23 (BRA), R24.2
3BRB: IC3.27 (BRB), R23.2
3CPI: C22.2, IC3.5 (CPI)
3CPO: C22.1, IC3.4 (CPO)
3DIAG: IC3.11 (DIAG), J11.1
3DIR: IC3.19 (DIR), J12.1, U1.31 (IO37)
3EN: IC3.2 (ENN), J12.8, R28.2, U1.29 (IO35)
3INDEX: IC3.12 (INDEX), J11.2
3MS1: IC3.9 (MS1), J12.7
3MS2: IC3.10 (MS2), J12.6
3OA1: IC3.24 (OA1), J10.4
3OA2: IC3.21 (OA2), J10.3
3OB1: IC3.26 (OB1), J10.5
3OB2: IC3.1 (OB2), J10.6
3PDN_UART: IC3.14 (PDN_UART), JMP2.2, R27.2
3STEP: IC3.16 (STEP), J12.2, U1.30 (IO36)
3VCP: C21.2, IC3.6 (VCP)
3VREF: IC3.17 (VREF), R19.2 (S), REF2.1
3VREF1: R19.1 (A), R26.1
45: U1.39 (STRAP/IO45)
46: U1.40 (STRAP/IO46)
+5V: C1.2, C6.2, C12.2, C13.2, C18.2, C19.2, C29.1, IC1.8 (5VOUT), IC1.15 (VCC_IO), IC2.8 (5VOUT), IC2.15 (VCC_IO), IC3.8 (5VOUT), IC3.15 (VCC_IO), J1.7, J7.7, J10.7, JP3.2, JP4.2, JP5.2, JP6.2, JP9.3, R7.2, R13.1, R20.2, R22.1, R26.2, R28.1, R32.1, U4.2 (VOUT)
A0: JP8.6, MOTOR1.3 (S), U1.20 (DAC_1/IO17)
A1: GPIO18PU.1, JP8.5, MOTOR2.3 (S), U1.21 (DAC_2/IO18)
A2: JP8.4, MOTOR3.3 (S), U1.17 (IO14)
A3: JP8.3, MOTOR4.3 (S), U1.12 (IO9)
A4: JP8.2, MOTOR5.3 (S), U1.10 (IO7)
A5: JP8.1, MOTOR6.3 (S), U1.8 (IO5)
CC1: J5.A5 (CC1), R12.2
CC2: J5.B5 (CC2), R11.2
CHIP_PU: C8.1, Q3.3 (C), R10.1, RESET.P$2, U1.41 (EN)
CLK: JP5.6, JP9.12, U1.15 (IO12)
CP210X_D+: IC4.4 (D+), JP1.3
CP210X_D-: IC4.5 (D-), JP2.1
CS: JP5.4, JP9.10, U1.13 (IO10)
DTR: IC4.28 (DTR), Q1.1 (E), R17.1
ESP32_D+: JP1.1, U1.23 (USB_D+/IO20)
ESP32_D-: JP2.3, U1.22 (USB_D-/IO19)
GND: C1.1, C2.2, C3.2, C4.1, C5.1, C6.1, C7.2, C7A1.2, C7A2.2, C7A3.2, C7B1.2, C7B2.2, C7B3.2, C8.2, C11.2, C12.1, C13.1, C14.2, C17.2, C18.1, C19.1, C20.2, C23.2, C24.2, C25.2, C26.2, C27.2, C28.2, C29.2, C30.1, C31.-, C32.-, C33.-, D1.C, D2.C, D3.C, D4.C, GPIO0.P$1, IC1.3 (GND), IC1.13 (CLK), IC1.18 (GND), IC1.TP (GND), IC2.3 (GND), IC2.13 (CLK), IC2.18 (GND), IC2.TP (GND), IC3.3 (GND), IC3.13 (CLK), IC3.18 (GND), IC3.TP (GND), IC4.3 (GND), IC4.EXP (GND), IC4.M (GND), J1.2, J1.8, J5.GND, J5.GND2 (GND), J7.2, J7.8, J10.2, J10.8, J13.2, J13.3, JP3.3, JP4.3, JP5.1, JP5.15, JP5.20, JP6.3, JP7.6, JP9.4, MOTOR1.5 (A), MOTOR2.5 (A), MOTOR3.5 (A), MOTOR4.5 (A), MOTOR5.5 (A), MOTOR6.5 (A), MT1.1, MT1.COM, MT1.S1 (SHIELD), MT1.S2 (SHIELD), R2.1, R3.1, R6.3 (E), R8.1, R9.1, R11.1, R12.1, R15.1, R16.1, R19.3 (E), R21.1, R23.1, R24.1, R27.1, R36.1, R37.3 (E), RESET.P$1, SUSPENDINV.1, U1.1 (GND), U1.26 (GND), U1.42 (GND), U1.GNDEP0 (GND), U1.GNDEP1 (GND), U1.GNDEP2 (GND), U1.GNDEP3 (GND), U1.GNDEP4 (GND), U1.GNDEP5 (GND), U1.GNDEP6 (GND), U1.GNDEP7 (GND), U1.GNDEP8 (GND), U2.1 (GND/ADJ), U3.1 (GND/ADJ), U4.1 (GND/ADJ)
KNOP1: C34.1, JP9.16, R36.2, S1.3, U1.35 (MTDI/IO41)
MOSI: JP5.5, JP9.11, U1.14 (IO11)
MTMS: U1.36 (MTMS/IO42)
unnamed: IC4.11 (!SUSPEND), R1.1
unnamed: D3.A, R4.2
unnamed: J5.A6 (D+), J5.B6 (D+), JP1.2
unnamed: IC4.8 (VBUS), R5.1, R9.2
unnamed: J5.A7 (D-), J5.B7 (D-), JP2.2
unnamed: C4.2, U1.18 (IO15/XTAL_32K_P), Y1.P$1 (1)
unnamed: C5.2, U1.19 (IO16/XTAL_32K_N), Y1.P$2 (2)
unnamed: J6.4, JMP1.1
unnamed: Q3.2 (B), R17.2
unnamed: J6.5, JMP1.3
unnamed: Q1.2 (B), R18.2
unnamed: J9.4, JMP3.1
unnamed: GPIO18PU.2, R14.1
unnamed: J9.5, JMP3.3
unnamed: J12.4, JMP2.1
unnamed: J12.5, JMP2.3
unnamed: IC4.9 (!RST), R29.1
unnamed: R1.2, SUSPENDINV.2
unnamed: D1.A, R30.2
unnamed: D2.A, R31.2
unnamed: D4.A, R32.2
NCKNOP: C34.2, SJ1.1
NCROTORY: C30.2, SJ2.1
ROTORA: JP9.7, MT1.A, R34.1, U1.6 (IO3)
ROTORB: JP9.8, MT1.B, R35.1, U1.7 (IO4)
ROTORKNOP: JP9.9, MT1.2, R33.1, SJ2.2, U1.9 (IO6)
RTS: IC4.24 (RTS), Q3.1 (E), R18.1
RX0: IC4.26 (TXD), JP7.3, U1.38 (U0RXD)
SCL: JP9.5, U1.5 (IO2)
SDA: JP9.6, U1.4 (IO1)
SERVO1: JP3.1, JP9.13, U1.32 (IO38)
SERVO2: JP4.1, JP9.14, U1.33 (MTCK/IO39)
SERVO3: JP6.1, JP9.15, U1.34 (MTDO/IO40)
TX0: IC4.25 (RXD), JP7.2, U1.37 (U0TXD)
VCC: C7.1, C7A1.1, C7A2.1, C7A3.1, C7B1.1, C7B2.1, C7B3.1, C9.1, C11.1, C14.1, C15.1, C17.1, C20.1, C21.1, C23.1, C26.1, C28.1, C31.+, C32.+, C33.+, IC1.22 (VS), IC1.28 (VS), IC2.22 (VS), IC2.28 (VS), IC3.22 (VS), IC3.28 (VS), J1.1, J7.1, J10.1, J13.1, J13.1-2 (1), JP9.1, U3.3 (VIN), U4.3 (VIN)
V_USB: C24.1, J5.VBUS1 (VBUS), J5.VBUS2 (VBUS), R5.2, U2.3 (VIN)

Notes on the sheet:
Espressif ESP32-S2
Module recommended VCC range: 3.0-3.6V
Optional pullup on GPIO18. Can be used to hold pin in known state during entry into download boot mode. See datasheet pg 19.
CP2104/2N (USB-to-Serial Converter)
USB Jumper LOW: CP210X (default) HIGH: ESP32-S2 native USB
GPIO13 LED
Reset Button
GPIO0 Button
Boot Mode Configuration Pin Default Boot Download GPIO0 1 1 0 GPIO45* x x x GPIO46 0 x 0 *GPIO45 sets SPI voltage, see DS pg 17. If GPIO45 and GPIO46 are floating, GPIO0 determines boot mode
Auto-Reset
If DTR is LOW, toggling RTS from HIGH to LOW resets to run mode. If RTS is HIGH, toggling DTR from LOW to HIGH resets to bootloader.
VRef 0...2.5V (0.11 Ohm sense resistor) >=2.50V 1.25V 0.50V EN (with pull-up) GND VCC PDN/UART (with pull-down) GND VCC optional
100% - 1.64A RMS 50% - 0.82A RMS 20% - 0.33A RMS driver enabled driver disabled automatic standstill current reduction automatic standstill power down disable UART interface
MS1 GND VIO GND VIO
MS2 GND GND VIO VIO
Steps 8 2 4 16
Interpolation Yes to 256 Yes to 256 Yes to 256 Yes to 256
ChopperMode stealthChop2 stealthChop2 stealthChop2 stealthChop2
To access all other modes (eg spreadCycle) you have to use the UART interface.
ST7920
HEADERS
LCD
DC-JACK
ROTARY ENCODER
FTDI
LDO'S
SERVO'S
NORMAL BUTTON
POTMETER
TMC2208

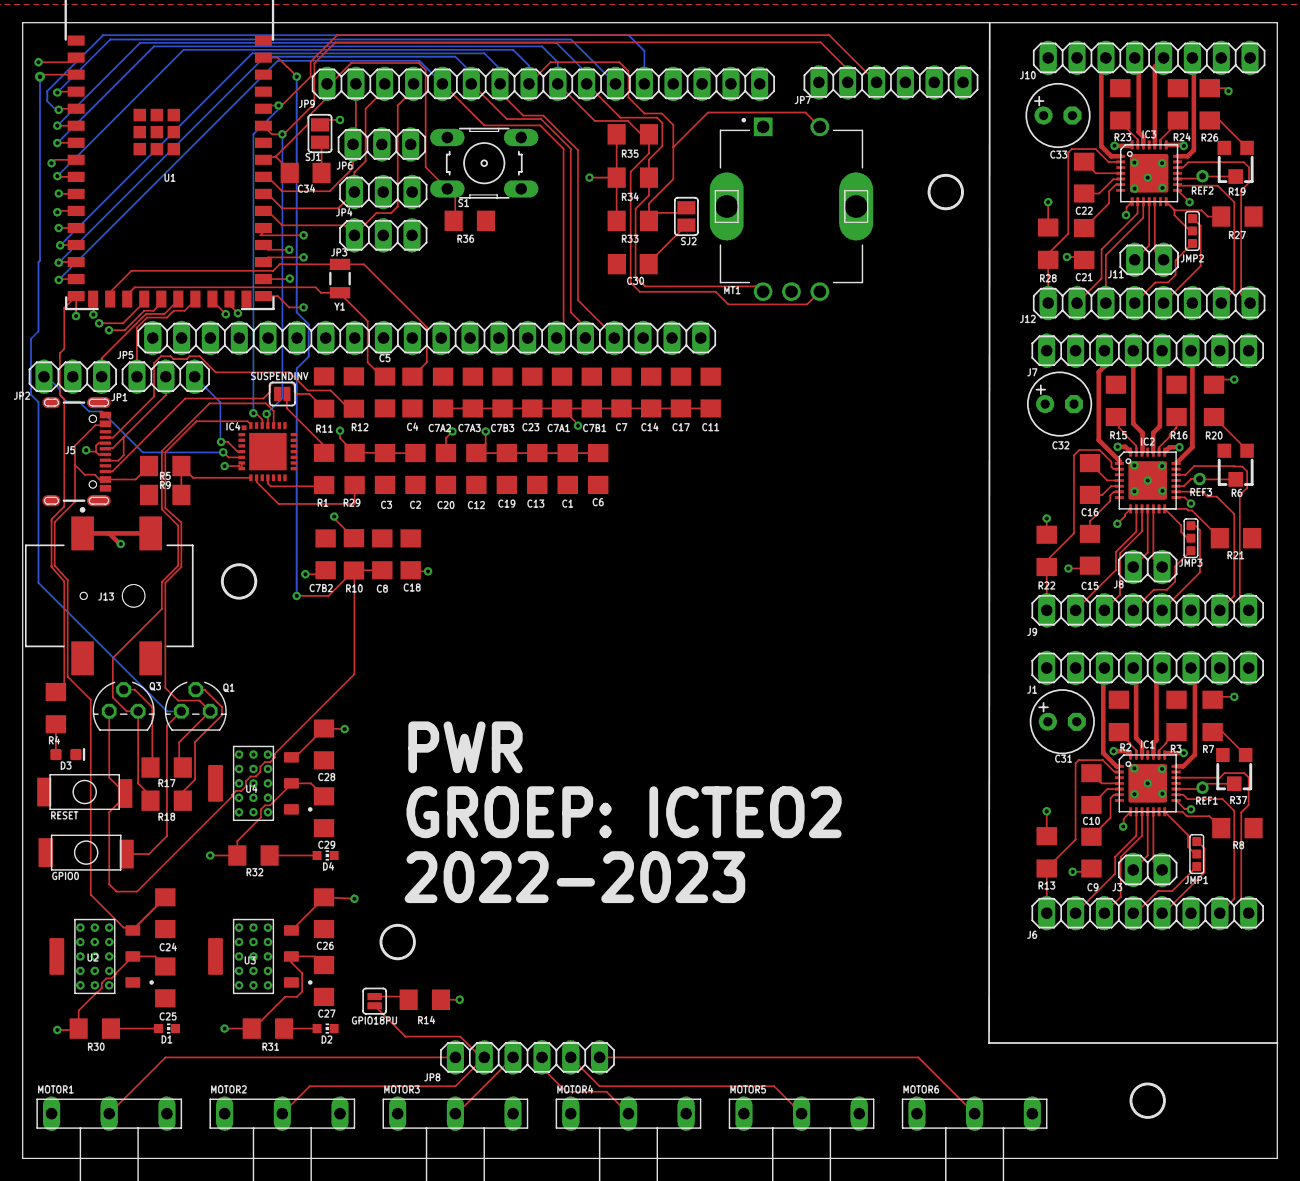
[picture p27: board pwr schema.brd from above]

Board: 4 copper layers, 110.5 x 100.0 mm, 136 parts (0 on the bottom side), 115 nets.

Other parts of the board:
U$1, U$2, U$3, U$4: 2,8

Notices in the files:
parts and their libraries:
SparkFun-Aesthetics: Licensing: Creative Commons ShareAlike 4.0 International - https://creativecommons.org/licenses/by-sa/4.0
